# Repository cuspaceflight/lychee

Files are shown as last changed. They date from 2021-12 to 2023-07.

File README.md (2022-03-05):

# Lychee

Lychee is a HAB (high-altitude balloon) which serves two main purposes:
- An induction project for new members looking to get hands-on building and launching a HAB.
- A test bed for prototype Martlet IV electronics.

## Motivation
After many years stuck in development hell, Project Strix (Martlet IV's avionics system) was ready for
hardware prototyping and flight testing. But flight testing avionics is difficult, especially on a budget;
so we decided to return to the society's roots and bring back our dormant HAB program.

With rough designs already complete for Martlet IV's eventual launch, we decided to port the flight
computer into a less modular form factor and consolidate modules, to create an extensible dual-board
architecture that allows us to test both fundamental system hardware and prototype future modules through
an expansion slot.

## Aims
The launch aims to test several key features and subsystems of the design ahead of construction of
final Project Strix flight hardware. In summary, these are:
- understand the embedded systems prototyping and development process for the STM32 + ChibiOS/RT stack
- perform real-time altimetry through a combination of
  - 2x redudant barometers
  - 1x 6-DoF IMU
  - 1x GPS
- relay telemetry through our custom ISM-band radio system
- verify the electrical performance of our 'blackbox' flight data recorder

## Using This Repository
This repository contains the electrical and software design files for the project. PCB designs were created
in KiCad 6, and the software was written for ChibiOS/RT. To install the dependency submodules, run
`git submodule update --init` from the root directory.

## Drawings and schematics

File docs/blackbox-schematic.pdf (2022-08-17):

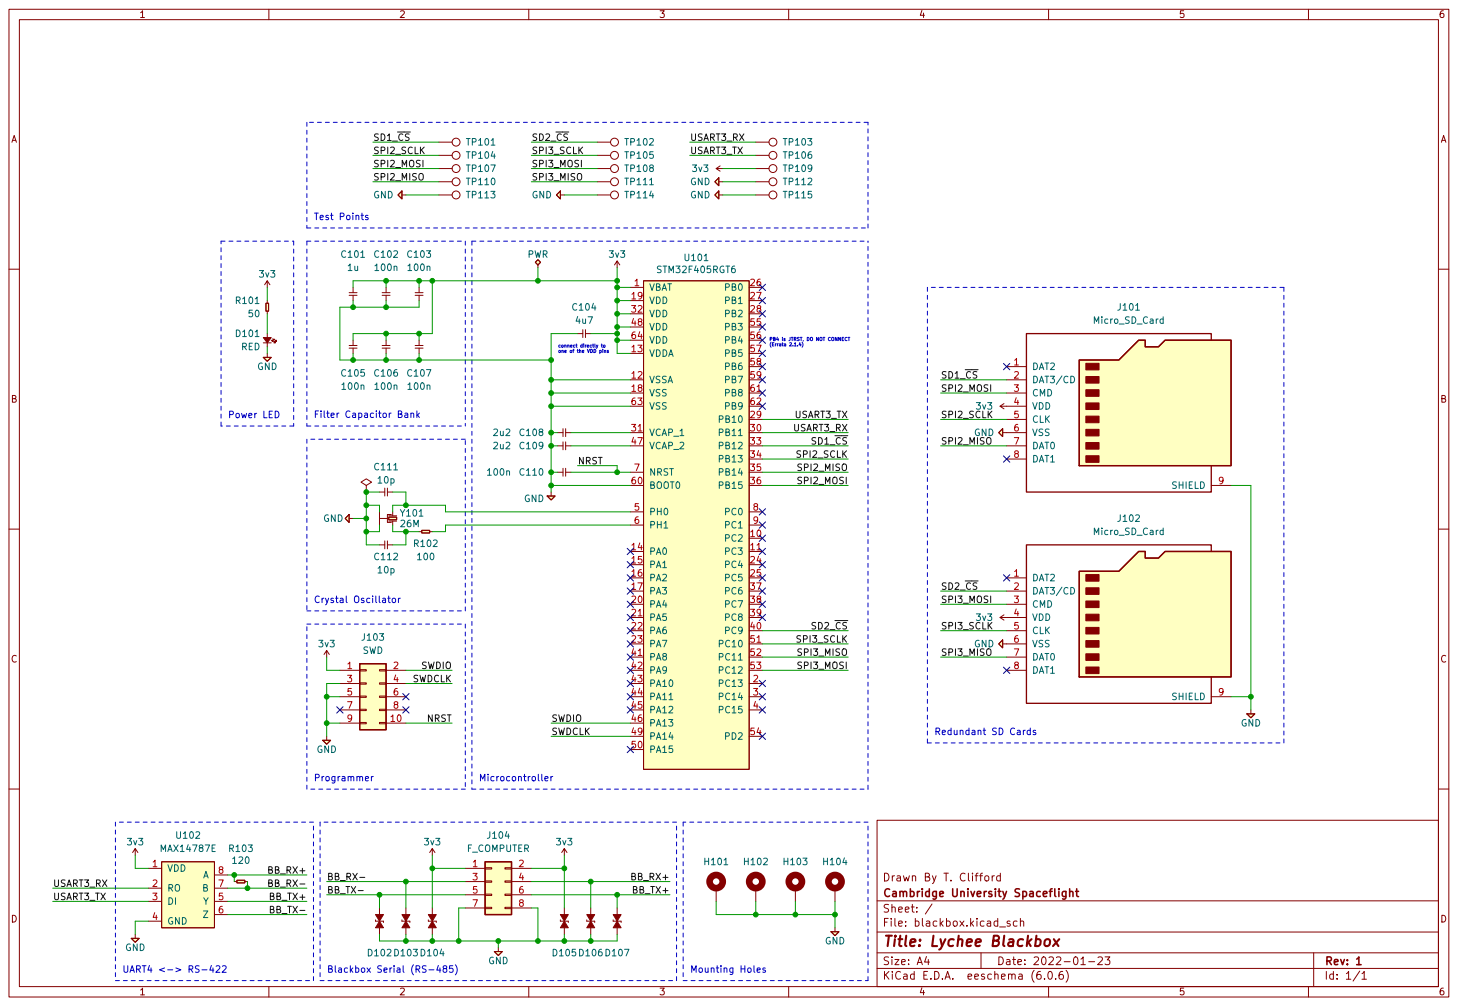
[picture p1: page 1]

PB4 is JTRST, DO NOT CONNECT

one of the VDD pins Power LED
100n GND

3 | | 4 6 8

Drawn By T. Clifford
File: blackbox.kicad_sch Sheet: / Cambridge University Spaceflight

Id: 1/1 Title: Lychee Blackbox

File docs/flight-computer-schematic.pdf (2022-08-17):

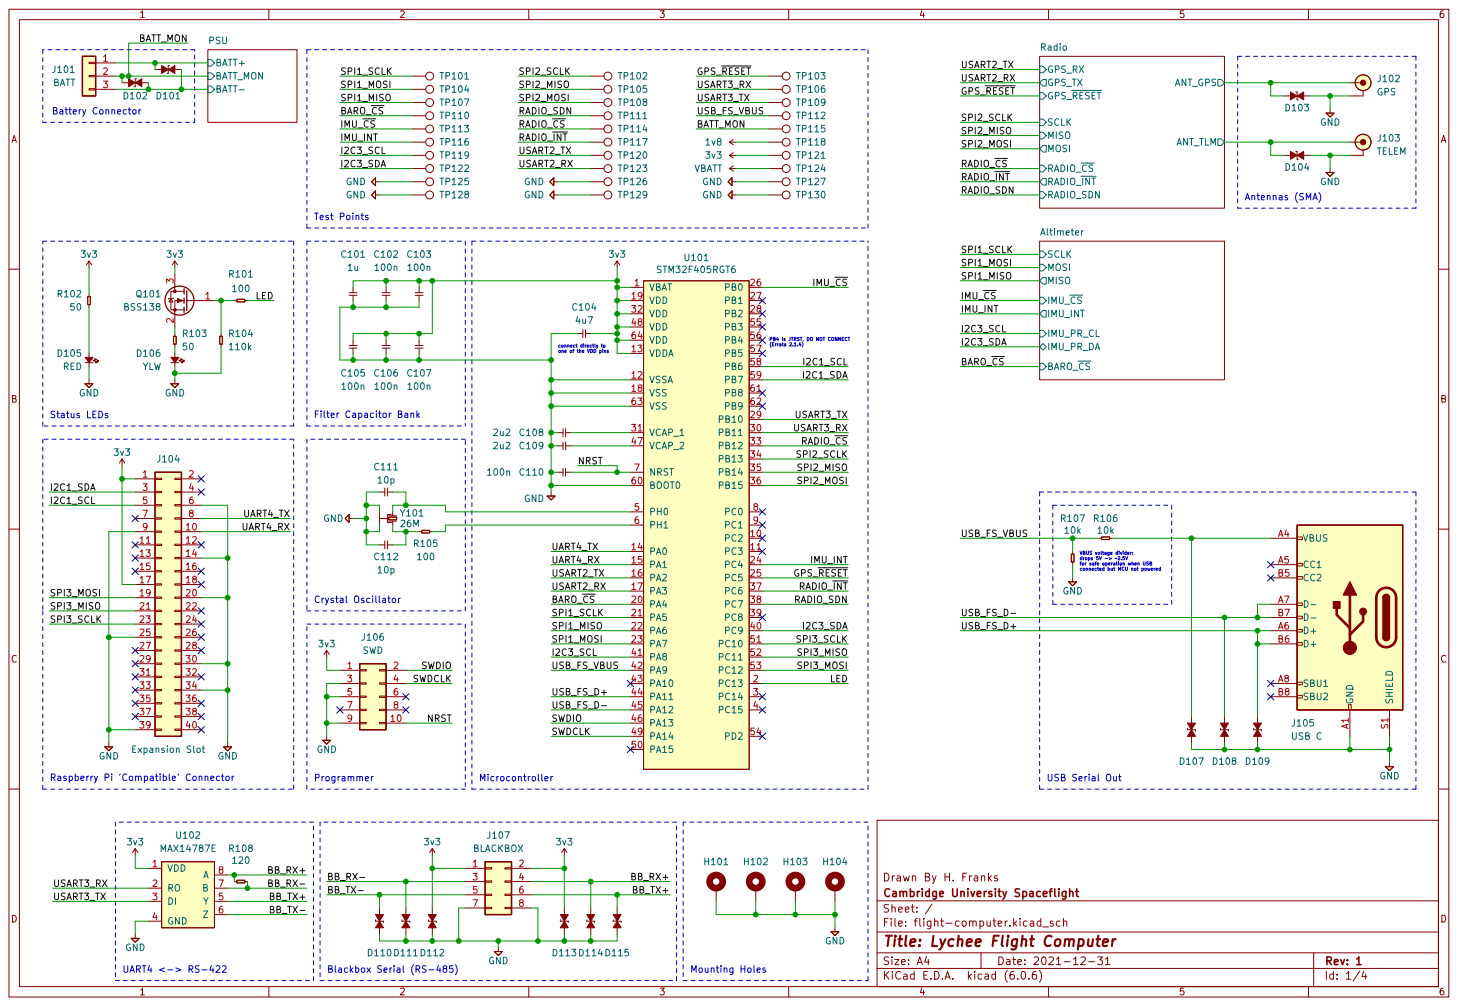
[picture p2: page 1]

SCLK MISO MOSI RADIO_~{INT} GPS_TX Radio BARO_~{CS}

RADIO_~{CS} SPI1_MOSI
Test Points Filter Capacitor Bank

(Errata 2.1.4) Raspberry Pi 'Compatible' Connector
D105 RED

PB4 is JTRST, DO NOT CONNECT

VBUS voltage divider: drops 5V -> ~2.5V

for safe operation when USB

connected but MCU not powered Crystal Oscillator

Drawn By H. Franks
File: flight-computer.kicad_sch Sheet: / Cambridge University Spaceflight

Id: 1/4 Title: Lychee Flight Computer

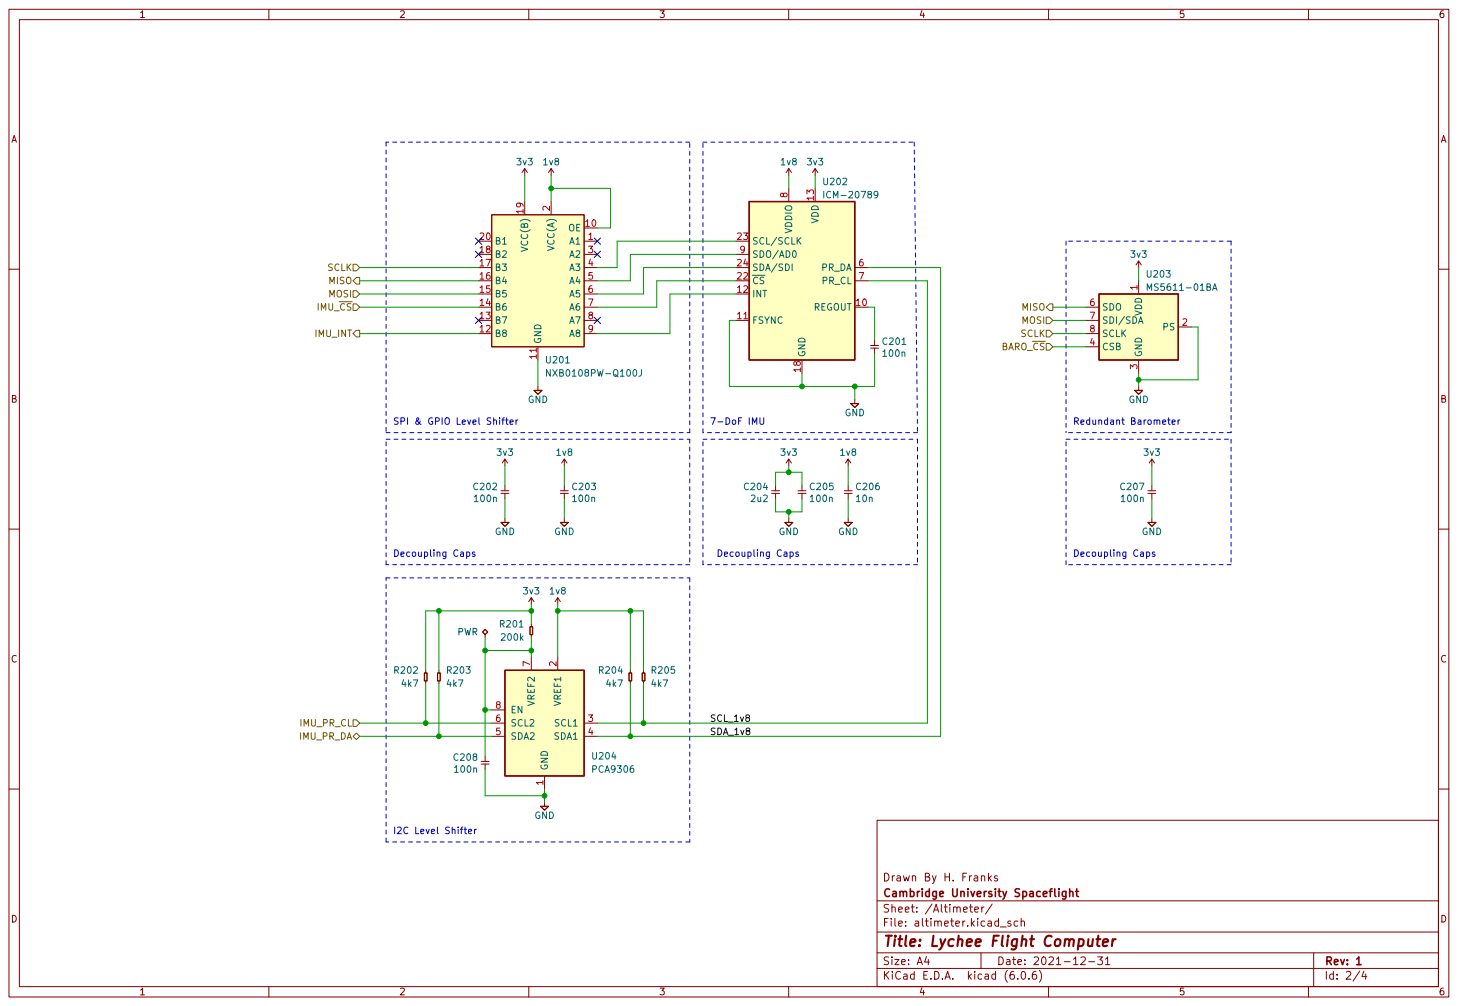
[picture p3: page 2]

3 CSB 4 SDO 6 SDI/SDA 7 SCLK 8 U203 MS5611-01BA REGOUT 10 FSYNC 11

Drawn By H. Franks
File: altimeter.kicad_sch Sheet: /Altimeter/ Cambridge University Spaceflight

Id: 2/4 Title: Lychee Flight Computer

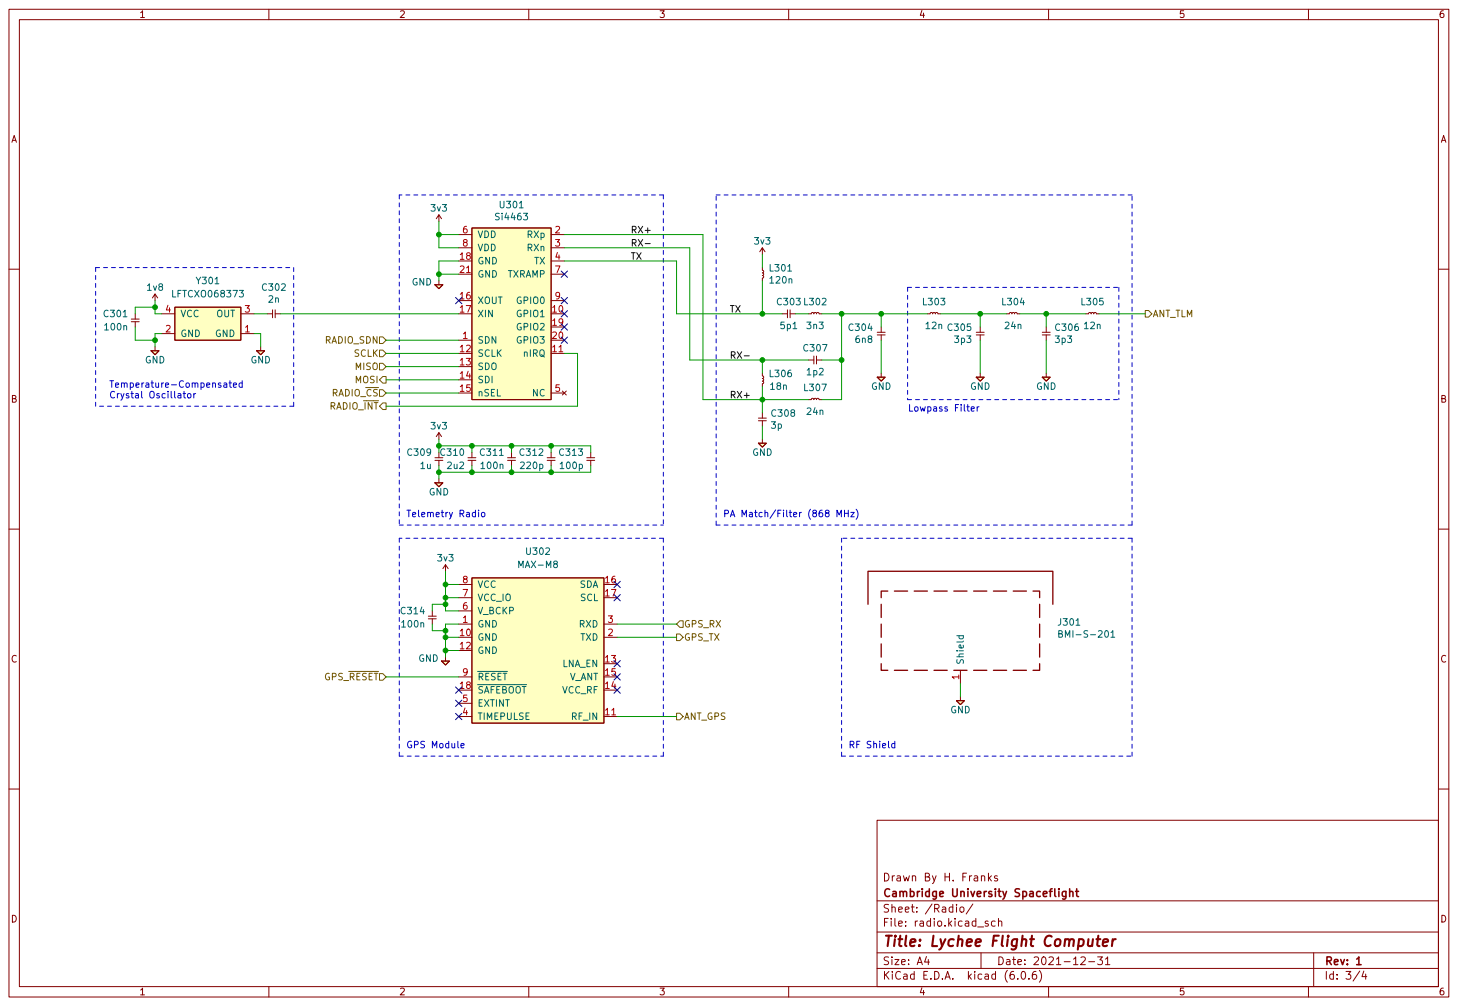
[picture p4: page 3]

TXRX- RX+ Telemetry Radio

Lowpass Filter RF Shield PA Match/Filter (868 MHz) GPS Module

Drawn By H. Franks
File: radio.kicad_sch Sheet: /Radio/ Cambridge University Spaceflight

Id: 3/4 Title: Lychee Flight Computer

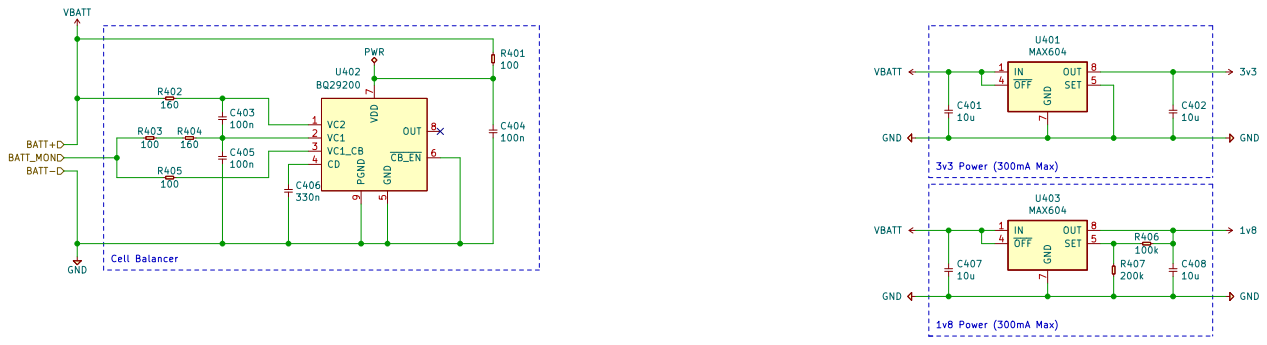
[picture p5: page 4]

File: psu.kicad_sch Sheet: /PSU/ Cambridge University Spaceflight

Id: 4/4 Title: Lychee Flight Computer

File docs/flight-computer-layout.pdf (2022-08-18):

MISO | MOSI | 0

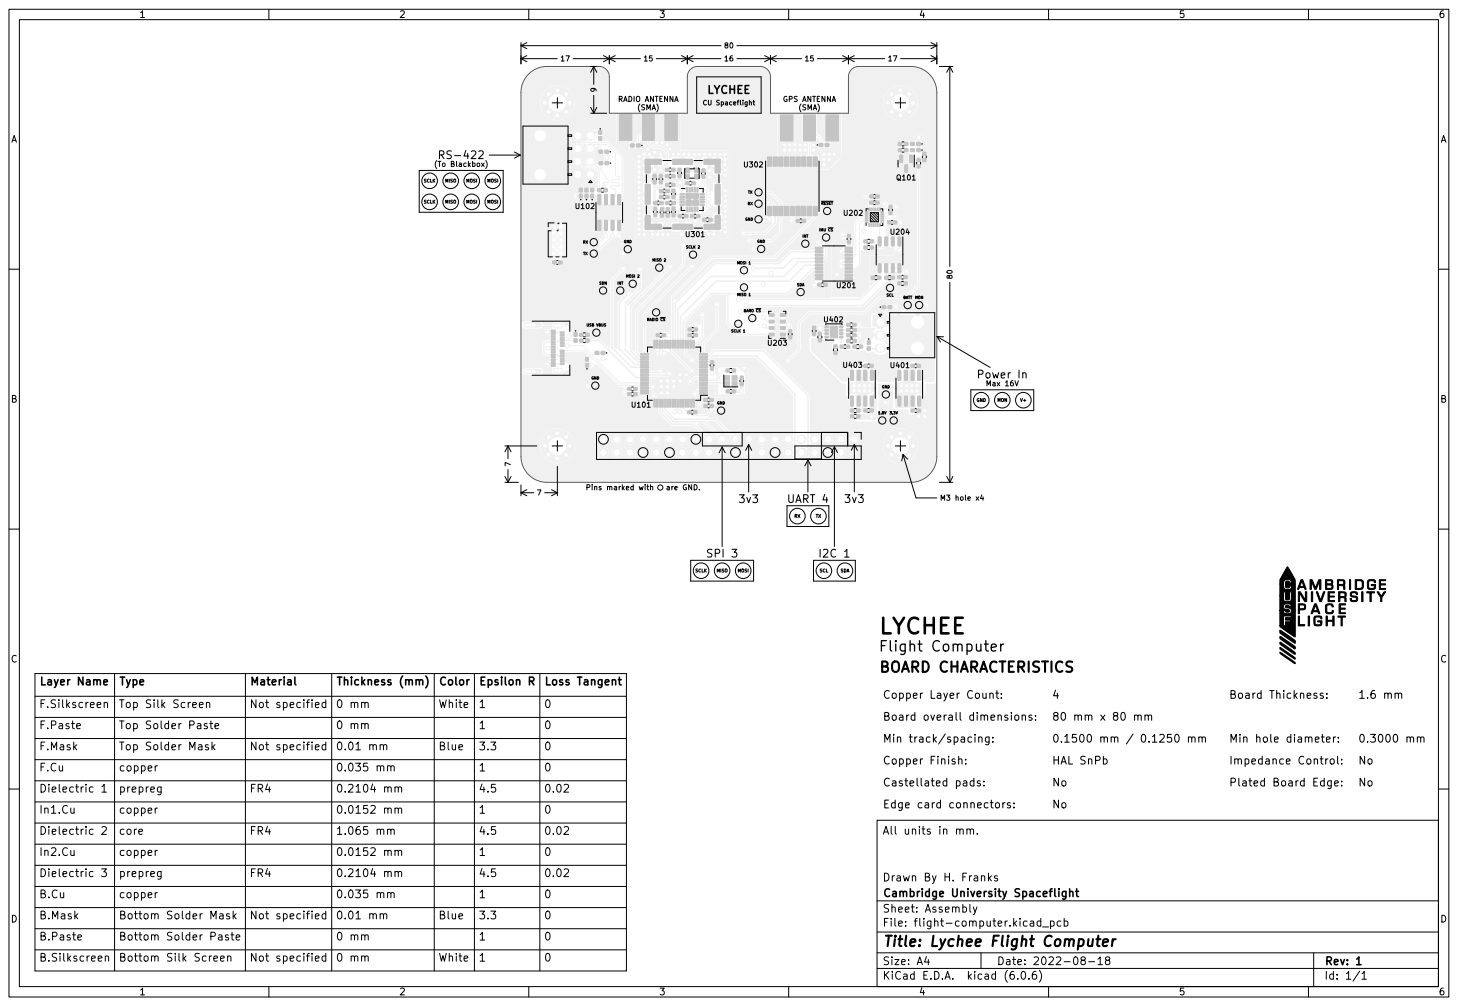
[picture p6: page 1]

CU Spaceflight
Pins marked with are GND. 1

MOSI Blue Top Solder Paste

0 Material Bottom Solder Paste
0 mm | | 1 Top Solder Mask

Thickness (mm) 0.01 mm | 1 FR4

Dielectric 1 | | 0.2104 mm | | 4.5
In1.Cu | copper | | White | | 0 | Drawn By H. Franks All units in mm. B.Paste
Dielectric 2 | | 1.065 mm | | 4.5

B.Mask | prepreg | | | 4.5 | 0.02

Cambridge University Spaceflight
Sheet: Assembly
File: flight-computer.kicad_pcb
Id: 1/1 Title: Lychee Flight Computer

0.035 mm | | | 0
0.01 mm | | 3.3 | 0

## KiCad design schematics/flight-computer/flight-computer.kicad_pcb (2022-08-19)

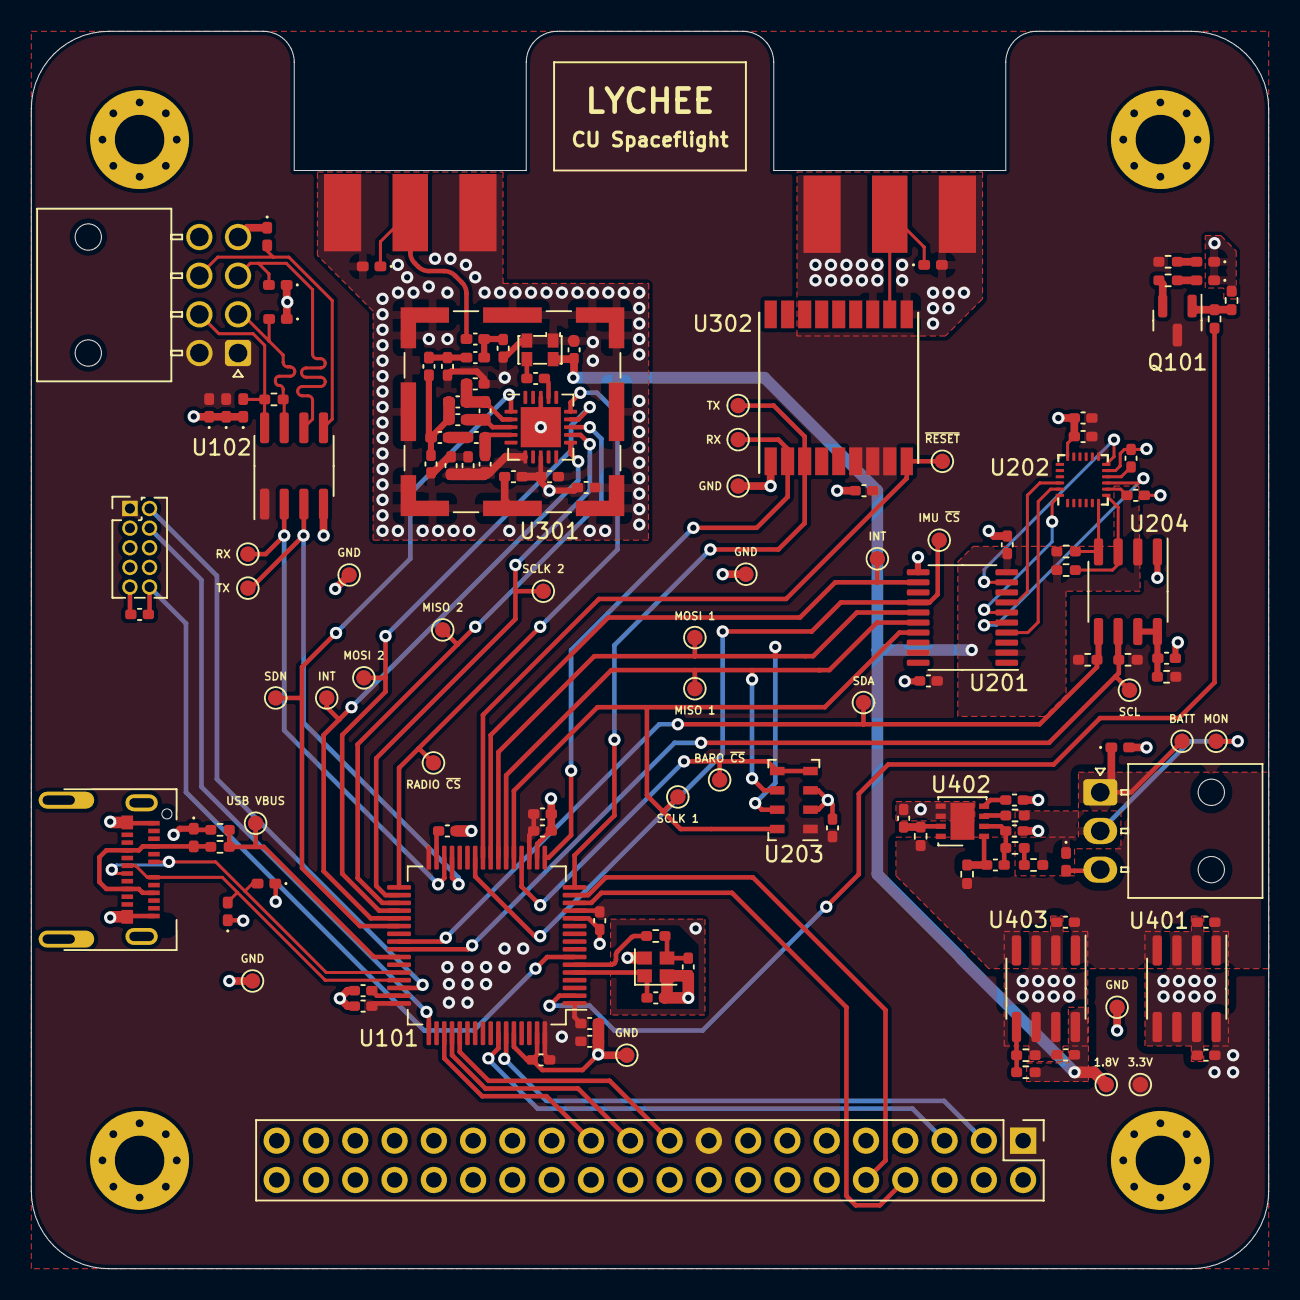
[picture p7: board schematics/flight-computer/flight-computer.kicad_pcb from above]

Board: 4 copper layers, 80.0 x 80.0 mm, 139 parts (0 on the bottom side), 79 nets.

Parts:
1.8V, 3.3V: TestPoint
BARO ~{CS}: TestPoint
BATT: TestPoint
C101: 1µ; C_0402
C102, C103, C105, C106, C107, C110, C201, C202, C203, C205, C207, C208, C301, C311, C314, C403, C404, C405: 100n; C_0402
C104: 4µ7; C_0402
C108, C109: 2µ2; C_0402
C111, C112: 10p; C_0402
C204, C310: 2u2; C_0402
C206: 10n; C_0402
C302: 2n; C_0402
C303: 5p1; C_0402
C304: 6n8; C_0402
C305, C306: 3p3; C_0402
C307: 1p2; C_0402
C308: 3p; C_0402
C309: 1u; C_0402
C312: 220p; C_0402
C313: 100p; C_0402
C401, C402, C407, C408: 10u; C_0402
C406: 330n; C_0402
D101, D102, D103, D104, D107, D108, D109, D110, D111, D112, D113, D114, D115: D_ESD; D_0402
D105: RED; LED_0402
D106: YLW; LED_0402
GND: TestPoint
GND#2, GND#3, GND#4, GND#5, GND#6: TestPoint
H101, H102, H103, H104: MountingHole_Pad
IMU ~{CS}: TestPoint
INT: TestPoint
INT#2: TestPoint
J101: BATT; Molex_Nano-Fit_105313-1103
J102: GPS; SMA-Edge
J103: TELEM; SMA-Edge
J104: Expansion Slot; Header_RaspberryPi
J105: USB C; USB_C
J106: SWD; Header_SWD
J107: BLACKBOX; Molex_Nano-Fit_105314-1108
J301: BMI-S-201
L301: 120n; L_0402
L302: 3n3; L_0402
L303, L305: 12n; L_0402
L304, L307: 24n; L_0402
L306: 18n; L_0402
MISO 1, MISO 2: TestPoint
MON: TestPoint
MOSI 1, MOSI 2: TestPoint
Q101: BSS138
R101, R105, R401, R403, R405: 100; R_0402
R102, R103: 50; R_0402
R104: 110k; R_0402
R106, R107: 10k; R_0402
R108: 120; R_0402
R201, R407: 200k; R_0402
R202, R203, R204, R205: 4k7; R_0402
R402, R404: 160; R_0402
R406: 100k; R_0402
RADIO ~{CS}: TestPoint
RX: TestPoint
RX#2: TestPoint
SCL: TestPoint
SCLK 1, SCLK 2: TestPoint
SDA: TestPoint
SDN: TestPoint
TX: TestPoint
TX#2: TestPoint
U101: STM32F405RGT6
U102: MAX14787E
U201: NXB0108PW-Q100J
U202: ICM-20789
U203: MS5611-01BA
U204: PCA9306
U301: Si4463
U302: MAX-M8
U401, U403: MAX604
U402: BQ29200
USB VBUS: TestPoint
Y101: 26M; Xtal_SMD_2016
Y301: LFTCXO068373

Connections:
1v8: 1.8V.1, C203.2, C206.2, C301.1, C408.1, R204.2, R205.2, R406.2, U201.2 (VCC(A)), U201.10 (OE), U202.8 (VDDIO), U204.2 (VREF1), U403.8 (OUT), Y301.4 (VCC)
3v3: 3.3V.1, C101.2, C102.2, C103.2, C104.2, C105.2, C106.2, C107.2, C202.2, C204.2, C205.2, C207.2, C309.1, C310.1, C311.1, C312.1, C313.1, C314.2, C402.1, D112.2, D113.2, J104.1, J104.17, J106.1, J107.1, J107.2, L301.1, Q101.3 (D), R102.2, R201.2, R202.2, R203.2, U101.1 (VBAT), U101.13 (VDDA), U101.19 (VDD), U101.32 (VDD), U101.48 (VDD), U101.64 (VDD), U102.1 (VDD), U201.19 (VCC(B)), U202.13 (VDD), U203.1 (VDD), U301.6 (VDD), U301.8 (VDD), U302.6 (V_BCKP), U302.7 (VCC_IO), U302.8 (VCC), U401.8 (OUT)
/Altimeter/SCL_1v8: R205.1, U202.7 (PR_CL), U204.3 (SCL1)
/Altimeter/SDA_1v8: R204.1, U202.6 (PR_DA), U204.4 (SDA1)
/BARO_~CS: BARO ~{CS}.1, U101.20 (PA4), U203.4 (CSB), U203.5 (CSB)
/BATT_MON: D102.1, J101.2, MON.1, R403.1, R405.1
/BB_RX+: D114.2, J107.4, R108.1, U102.8 (A)
/BB_RX-: D111.2, J107.3, R108.2, U102.7 (B)
/BB_TX+: D115.2, J107.6, U102.5 (Y)
/BB_TX-: D110.2, J107.5, U102.6 (Z)
/GPS_~RESET: U101.25 (PC5), U302.9 (~RESET)
/I2C1_SCL: J104.5, U101.58 (PB6)
/I2C1_SDA: J104.3, U101.59 (PB7)
/I2C3_SCL: R202.1, SCL.1, U101.41 (PA8), U204.6 (SCL2)
/I2C3_SDA: R203.1, SDA.1, U101.40 (PC9), U204.5 (SDA2)
/IMU_INT: INT#2.1, U101.24 (PC4), U201.12 (B8)
/IMU_~CS: IMU ~{CS}.1, U101.26 (PB0), U201.14 (B6)
/LED: R101.1, U101.2 (PC13)
/NRST: C110.2, J106.10, U101.7 (NRST)
/RADIO_SDN: SDN.1, U101.38 (PC7), U301.1 (SDN)
/RADIO_~CS: RADIO ~{CS}.1, U101.33 (PB12), U301.15 (nSEL)
/RADIO_~INT: INT.1, U101.37 (PC6), U301.11 (nIRQ)
/Radio/ANT_GPS: D103.1, J102.1 (RF), U302.11 (RF_IN)
/Radio/ANT_TLM: D104.1, J103.1 (RF), L305.2
/Radio/RX+: C308.1, L306.2, L307.1, U301.2 (RXp)
/Radio/RX-: C307.1, L306.1, U301.3 (RXn)
/Radio/TX: C303.1, L301.2, U301.4 (TX)
/SPI1_MISO: MISO 1.1, U101.22 (PA6), U201.16 (B4), U203.6 (SDO)
/SPI1_MOSI: MOSI 1.1, U101.23 (PA7), U201.15 (B5), U203.7 (SDI/SDA)
/SPI1_SCLK: SCLK 1.1, U101.21 (PA5), U201.17 (B3), U203.8 (SCLK)
/SPI2_MISO: MISO 2.1, U101.35 (PB14), U301.13 (SDO)
/SPI2_MOSI: MOSI 2.1, U101.36 (PB15), U301.14 (SDI)
/SPI2_SCLK: SCLK 2.1, U101.34 (PB13), U301.12 (SCLK)
/SPI3_MISO: J104.21, U101.52 (PC11)
/SPI3_MOSI: J104.19, U101.53 (PC12)
/SPI3_SCLK: J104.23, U101.51 (PC10)
/SWDCLK: J106.4, U101.49 (PA14)
/SWDIO: J106.2, U101.46 (PA13)
/UART4_RX: J104.10, U101.15 (PA1)
/UART4_TX: J104.8, U101.14 (PA0)
/USART2_RX: RX#2.1, U101.17 (PA3), U302.2 (TXD)
/USART2_TX: TX.1, U101.16 (PA2), U302.3 (RXD)
/USART3_RX: RX.1, U101.30 (PB11), U102.2 (RO)
/USART3_TX: TX#2.1, U101.29 (PB10), U102.3 (DI)
/USB_FS_D+: D109.2, J105.A6 (D+), J105.B6 (D+), U101.44 (PA11)
/USB_FS_D-: D108.2, J105.A7 (D-), J105.B7 (D-), U101.45 (PA12)
/USB_FS_VBUS: R106.1, R107.2, U101.42 (PA9), USB VBUS.1
GND: C101.1, C102.1, C103.1, C104.1, C105.1, C106.1, C107.1, C108.1, C109.1, C110.1, C111.1, C112.1, C201.1, C202.1, C203.1, C204.1, C205.1, C206.1, C207.1, C208.1, C301.2, C304.2, C305.2, C306.2, C308.2, C309.2, C310.2, C311.2, C312.2, C313.2, C314.1, C401.2, C402.2, C404.2, C405.2, C406.2, C407.2, C408.2, D101.2, D102.2, D103.2, D104.2, D105.1, D106.1, D107.1, D108.1, D109.1, D110.1, D111.1, D112.1, D113.1, D114.1, D115.1, GND.1, GND#2.1, GND#3.1, GND#4.1, GND#5.1, GND#6.1, H101.1, H102.1, H103.1, H104.1, J101.3, J102.2 (GND), J103.2 (GND), J104.6, J104.9, J104.14, J104.20, J104.25, J104.30, J104.34, J104.39, J105.A1 (GND), J105.A12 (GND), J105.B1 (GND), J105.B12 (GND), J105.S1 (SHIELD), J106.3, J106.5, J106.9, J107.7, J107.8, J301.1 (Shield), R104.1, R107.1, R407.2, U101.12 (VSSA), U101.18 (VSS), U101.60 (BOOT0), U101.63 (VSS), U102.4 (GND), U201.11 (GND), U202.11 (FSYNC), U202.18 (GND), U203.2 (PS), U203.3 (GND), U204.1 (GND), U301.18 (GND), U301.21 (GND), U302.1 (GND), U302.10 (GND), U302.12 (GND), U401.2 (GND), U401.3 (GND), U401.5 (SET), U401.6 (GND), U401.7 (GND), U402.5 (GND), U402.6 (~CB_EN), U402.9 (PGND), U403.2 (GND), U403.3 (GND), U403.6 (GND), U403.7 (GND), Y101.2, Y101.4, Y301.1 (GND), Y301.2 (GND)
unnamed: C108.2, U101.31 (VCAP_1)
unnamed: C109.2, U101.47 (VCAP_2)
unnamed: C111.2, U101.5 (PH0), Y101.1
unnamed: C112.2, R105.1, Y101.3
unnamed: C201.2, U202.10 (REGOUT)
unnamed: C208.2, R201.1, U204.7 (VREF2), U204.8 (EN)
unnamed: C302.1, Y301.3 (OUT)
unnamed: C302.2, U301.17 (XIN)
unnamed: C303.2, L302.1
unnamed: C304.1, C307.2, L302.2, L303.1, L307.2
unnamed: C305.1, L303.2, L304.1
unnamed: C306.1, L304.2, L305.1
unnamed: C403.1, R402.2, U402.1 (VC2)
unnamed: C403.2, C405.1, R404.2, U402.2 (VC1)
unnamed: C404.1, R401.2, U402.7 (VDD)
unnamed: C406.1, U402.4 (CD)
unnamed: D105.2, R102.1
unnamed: D106.2, R103.1
unnamed: D107.2, J105.A4 (VBUS), J105.A9 (VBUS), J105.B4 (VBUS), J105.B9 (VBUS), R106.2
unnamed: Q101.1 (G), R101.2, R104.2
unnamed: Q101.2 (S), R103.2
unnamed: R105.2, U101.6 (PH1)
unnamed: R403.2, R404.1
unnamed: R405.2, U402.3 (VC1_CB)
unnamed: R406.1, R407.1, U403.5 (SET)
unnamed: U201.4 (A3), U202.23 (SCL/SCLK)
unnamed: U201.5 (A4), U202.9 (SDO/AD0)
unnamed: U201.6 (A5), U202.24 (SDA/SDI)
unnamed: U201.7 (A6), U202.22 (~CS)
unnamed: U201.9 (A8), U202.12 (INT)
VBATT: BATT.1, C401.1, C407.1, D101.1, J101.1, R401.1, R402.1, U401.1 (IN), U401.4 (~OFF), U403.1 (IN), U403.4 (~OFF)

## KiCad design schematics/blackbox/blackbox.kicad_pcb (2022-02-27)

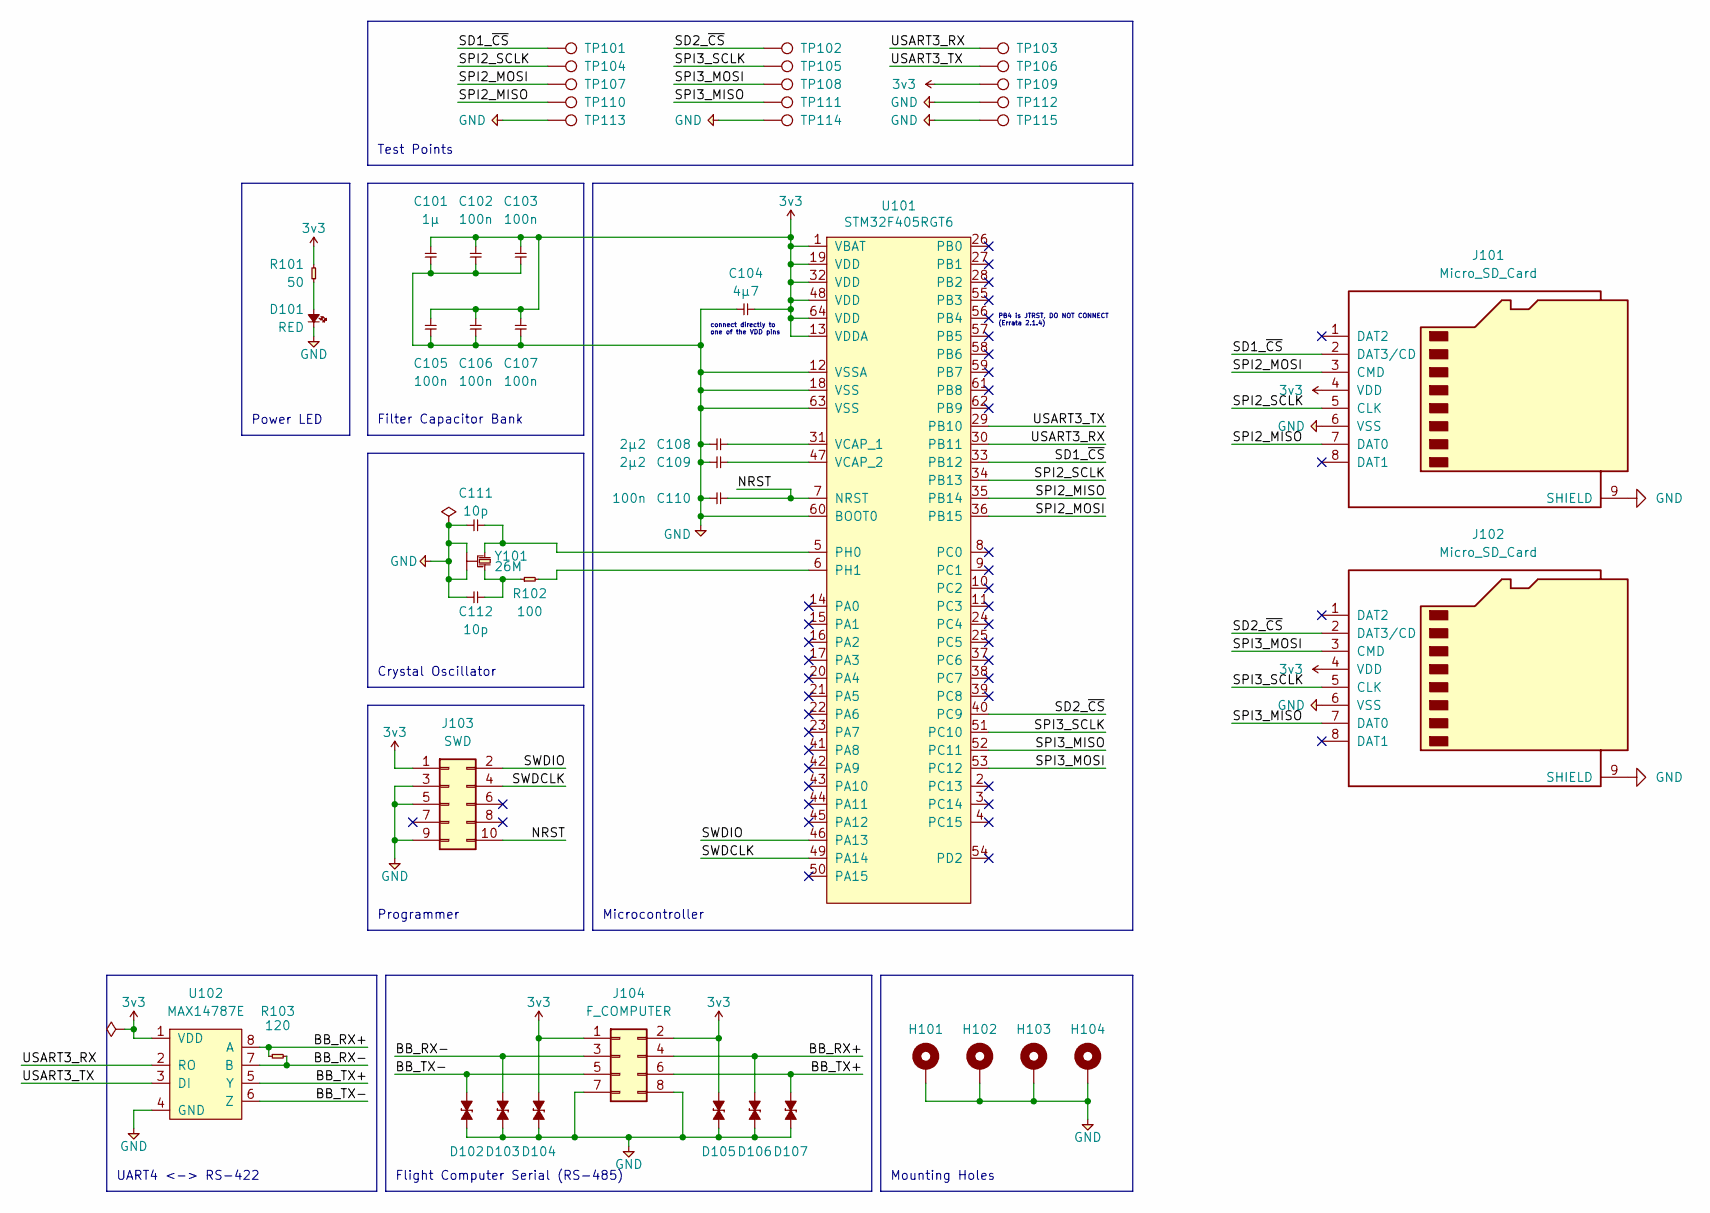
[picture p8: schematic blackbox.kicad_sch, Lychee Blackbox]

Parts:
C101: 1µ; C_0402; Farnell 1759436
C102, C103, C105, C106, C107, C110: 100n; C_0402; Farnell 2496771
C104: 4µ7; C_0402; Farnell 2211173
C108, C109: 2µ2; C_0402; Farnell 2362088
C111, C112: 10p; C_0402; Farnell 2494183
D101: RED; LED_0402; Farnell 3796306
D102, D103, D104, D105, D106, D107: D_ESD; D_0402; Farnell 2368169
H101, H102, H103, H104: MountingHole_Pad
J101, J102: Micro_SD_Card; microSD_HC_Wuerth_693072010801; Farnell 1344008
J103: SWD; Header_SWD; Farnell 2856426
J104: F_COMPUTER; Molex_Nano-Fit_105314-1108
R101: 50; R_0402; Farnell 3544456
R102: 100; R_0402; Farnell 2447095
R103: 120; R_0402; Farnell 2447103
TP101, TP102, TP103, TP104, TP105, TP106, TP107, TP108, TP109, TP110, TP111, TP112, TP113, TP114, TP115: TestPoint
U101: STM32F405RGT6; Farnell 2064363
U102: MAX14787E; Farnell 2528531
Y101: 26M; Xtal_SMD_2016; Farnell 2506952

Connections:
3v3: C101.2, C102.2, C103.2, C104.2, C105.2, C106.2, C107.2, D104.2, D105.2, J101.4 (VDD), J102.4 (VDD), J103.1, J104.1, J104.2, R101.2, TP109.1, U101.1 (VBAT), U101.13 (VDDA), U101.19 (VDD), U101.32 (VDD), U101.48 (VDD), U101.64 (VDD), U102.1 (VDD)
/BB_RX+: D106.2, J104.4, R103.1, U102.8 (A)
/BB_RX-: D103.2, J104.3, R103.2, U102.7 (B)
/BB_TX+: D107.2, J104.6, U102.5 (Y)
/BB_TX-: D102.2, J104.5, U102.6 (Z)
/NRST: C110.2, J103.10, U101.7 (NRST)
/SD1_~CS: J101.2 (DAT3/CD), TP101.1, U101.33 (PB12)
/SD2_~CS: J102.2 (DAT3/CD), TP102.1, U101.40 (PC9)
/SPI2_MISO: J101.7 (DAT0), TP110.1, U101.35 (PB14)
/SPI2_MOSI: J101.3 (CMD), TP107.1, U101.36 (PB15)
/SPI2_SCLK: J101.5 (CLK), TP104.1, U101.34 (PB13)
/SPI3_MISO: J102.7 (DAT0), TP111.1, U101.52 (PC11)
/SPI3_MOSI: J102.3 (CMD), TP108.1, U101.53 (PC12)
/SPI3_SCLK: J102.5 (CLK), TP105.1, U101.51 (PC10)
/SWDCLK: J103.4, U101.49 (PA14)
/SWDIO: J103.2, U101.46 (PA13)
/USART3_RX: TP103.1, U101.30 (PB11), U102.2 (RO)
/USART3_TX: TP106.1, U101.29 (PB10), U102.3 (DI)
GND: C101.1, C102.1, C103.1, C104.1, C105.1, C106.1, C107.1, C108.1, C109.1, C110.1, C111.1, C112.1, D101.1, D102.1, D103.1, D104.1, D105.1, D106.1, D107.1, H101.1, H102.1, H103.1, H104.1, J101.6 (VSS), J101.9 (SHIELD), J102.6 (VSS), J102.9 (SHIELD), J103.3, J103.5, J103.9, J104.7, J104.8, TP112.1, TP113.1, TP114.1, TP115.1, U101.12 (VSSA), U101.18 (VSS), U101.60 (BOOT0), U101.63 (VSS), U102.4 (GND), Y101.2, Y101.4
unnamed: C108.2, U101.31 (VCAP_1)
unnamed: C109.2, U101.47 (VCAP_2)
unnamed: C111.2, U101.5 (PH0), Y101.1
unnamed: C112.2, R102.1, Y101.3
unnamed: D101.2, R101.1
unnamed: R102.2, U101.6 (PH1)

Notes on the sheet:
Flight Computer Serial (RS-485)
Power LED
Filter Capacitor Bank
PB4 is JTRST, DO NOT CONNECT (Errata 2.1.4)
Mounting Holes
Test Points
Crystal Oscillator
UART4 <-> RS-422
Programmer
connect directly to one of the VDD pins
Microcontroller

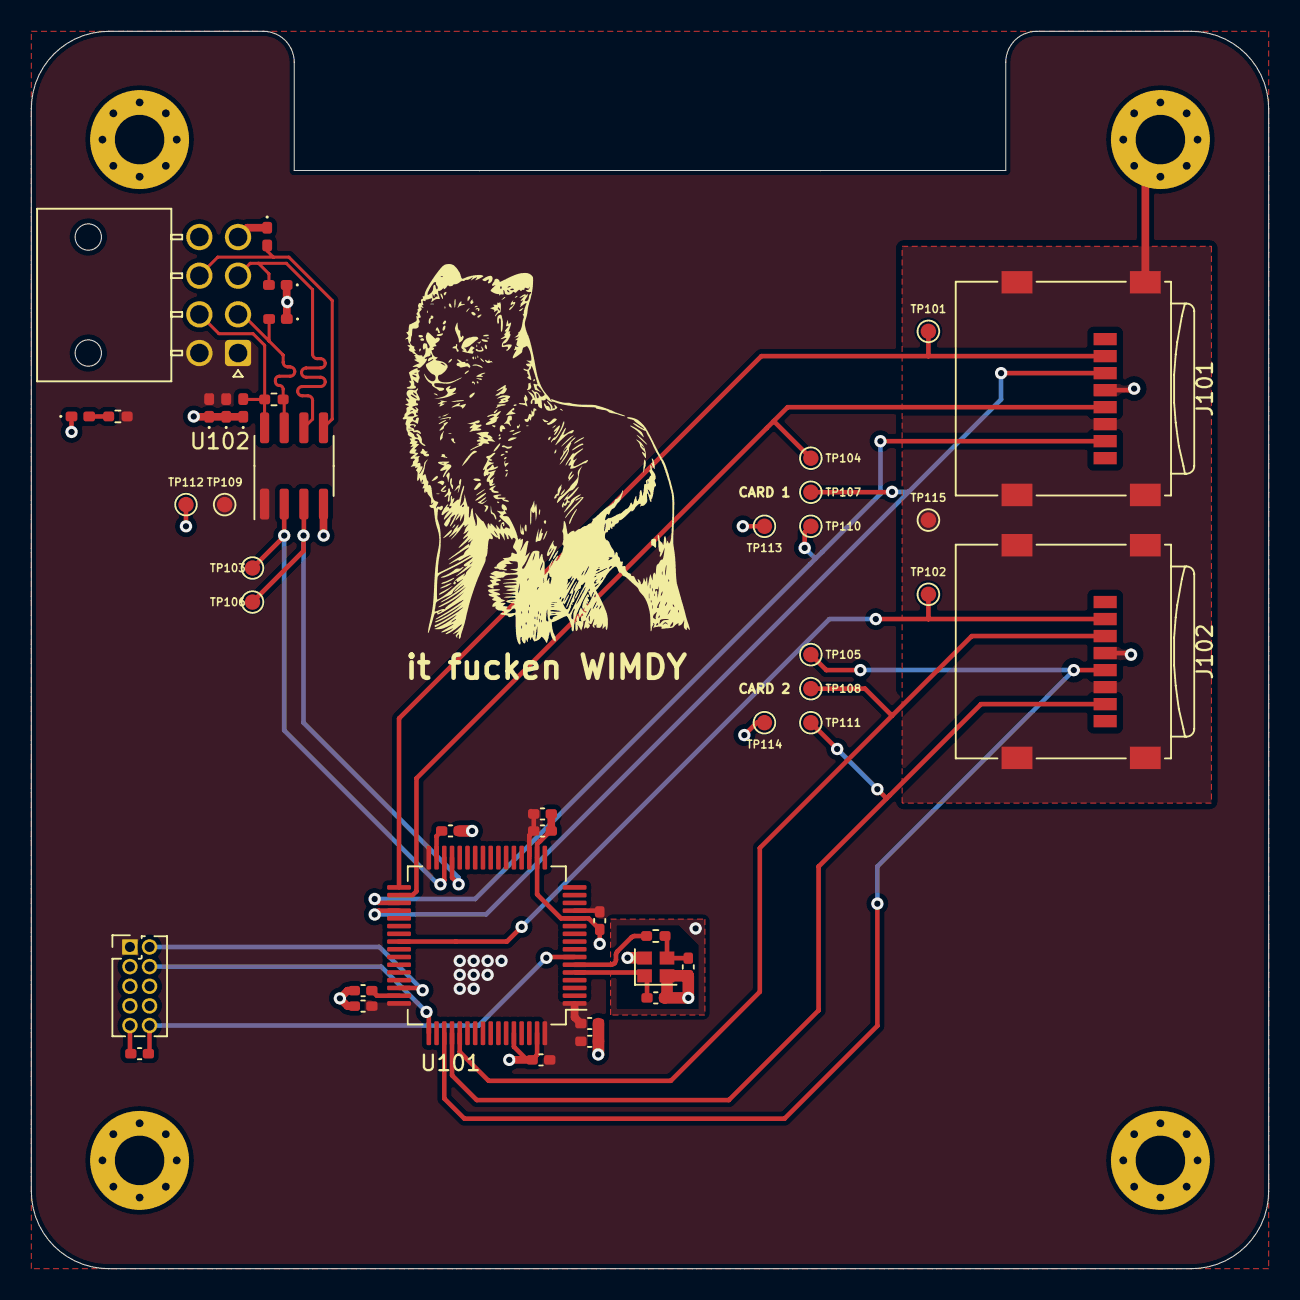
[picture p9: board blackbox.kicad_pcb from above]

Board: 4 copper layers, 80.0 x 80.0 mm, 48 parts (0 on the bottom side), 25 nets.

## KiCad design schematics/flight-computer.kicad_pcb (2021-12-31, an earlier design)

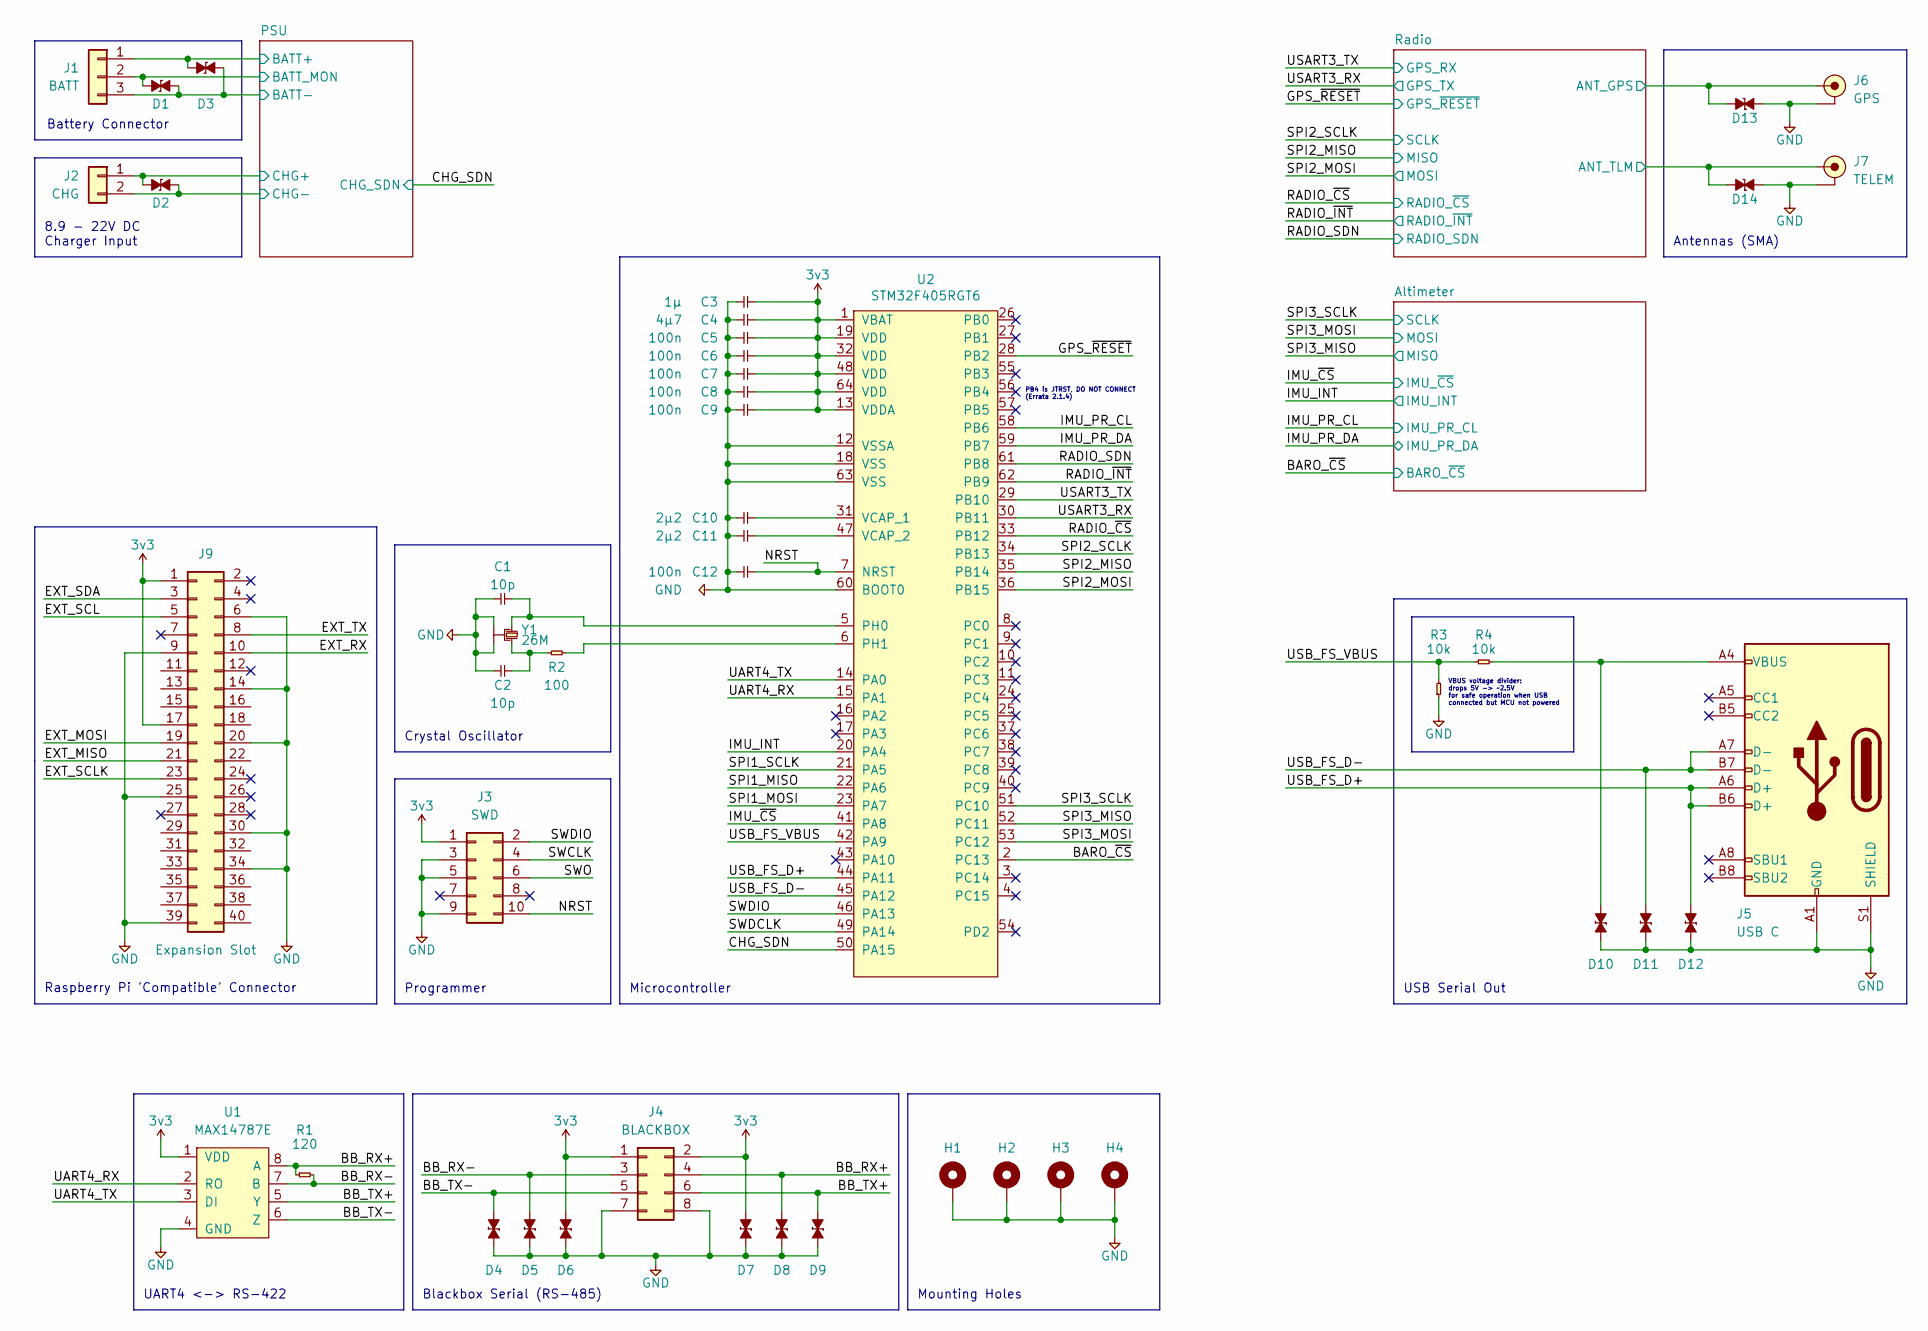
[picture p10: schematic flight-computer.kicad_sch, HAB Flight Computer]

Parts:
C1, C2: 10p; C_0402
C3: 1µ; C_0402; Farnell 2496814
C4: 4µ7; C_0402; Farnell 2426952
C5, C6, C7, C8, C9, C12: 100n; C_0402; Farnell 2496771
C10, C11: 2µ2; C_0402; Farnell 2362088
D1, D2, D3, D4, D5, D6, D7, D8, D9, D10, D11, D12, D13, D14: D_ESD; D_0402; Farnell 2368169
H1, H2, H3, H4: MountingHole_Pad
J1: BATT; Molex_Nano-Fit_105313-1103; Farnell 2820685
J2: CHG; Molex_Nano-Fit_105313-1102
J3: SWD; Header_SWD
J4: BLACKBOX; Molex_Nano-Fit_105314-1108
J5: USB C; USB_C; Farnell 2990003
J6: GPS; SMA-Edge; Farnell 1608592
J7: TELEM; SMA-Edge; Farnell 1608592
J9: Expansion Slot; Header_RaspberryPi
R1: 120; R_0402
R2: 100; R_0402
R3, R4: 10k; R_0402
U1: MAX14787E; Farnell 2528531
U2: STM32F405RGT6; Farnell 2064363
Y1: 26M; Xtal-20x16; Farnell 2506952

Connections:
3v3: C3.2, C4.2, C5.2, C6.2, C7.2, C8.2, C9.2, D6.2, D7.2, J3.1, J4.1, J4.2, J9.1, J9.17, U1.1 (VDD), U2.1 (VBAT), U2.13 (VDDA), U2.19 (VDD), U2.32 (VDD), U2.48 (VDD), U2.64 (VDD); also elsewhere on the board
/BARO_~CS: U2.2 (PC13); also elsewhere on the board
/BB_RX+: D8.2, J4.4, R1.1, U1.8 (A)
/BB_RX-: D5.2, J4.3, R1.2, U1.7 (B)
/BB_TX+: D9.2, J4.6, U1.5 (Y)
/BB_TX-: D4.2, J4.5, U1.6 (Z)
/CHG_SDN: U2.50 (PA15); also elsewhere on the board
/EXT_MISO: J9.21
/EXT_MOSI: J9.19
/EXT_RX: J9.10
/EXT_SCL: J9.5
/EXT_SCLK: J9.23
/EXT_SDA: J9.3
/EXT_TX: J9.8
/GPS_~RESET: U2.28 (PB2); also elsewhere on the board
/IMU_INT: U2.20 (PA4); also elsewhere on the board
/IMU_PR_CL: U2.58 (PB6); also elsewhere on the board
/IMU_PR_DA: U2.59 (PB7); also elsewhere on the board
/IMU_~CS: U2.41 (PA8); also elsewhere on the board
/NRST: C12.2, J3.10, U2.7 (NRST)
/PSU/BATT_MON: D1.1, J1.2; also elsewhere on the board
/PSU/CHG+: D2.1, J2.1; also elsewhere on the board
/RADIO_SDN: U2.61 (PB8); also elsewhere on the board
/RADIO_~CS: U2.33 (PB12); also elsewhere on the board
/RADIO_~INT: U2.62 (PB9); also elsewhere on the board
/Radio/ANT_GPS: D13.1, J6.1 (RF); also elsewhere on the board
/Radio/ANT_TLM: D14.1, J7.1 (RF); also elsewhere on the board
/SPI1_MISO: U2.22 (PA6)
/SPI1_MOSI: U2.23 (PA7)
/SPI1_SCLK: U2.21 (PA5)
/SPI2_MISO: U2.35 (PB14); also elsewhere on the board
/SPI2_MOSI: U2.36 (PB15); also elsewhere on the board
/SPI2_SCLK: U2.34 (PB13); also elsewhere on the board
/SPI3_MISO: U2.52 (PC11); also elsewhere on the board
/SPI3_MOSI: U2.53 (PC12); also elsewhere on the board
/SPI3_SCLK: U2.51 (PC10); also elsewhere on the board
/SWCLK: J3.4
/SWDCLK: U2.49 (PA14)
/SWDIO: J3.2, U2.46 (PA13)
/SWO: J3.6
/UART4_RX: U1.2 (RO), U2.15 (PA1)
/UART4_TX: U1.3 (DI), U2.14 (PA0)
/USART3_RX: U2.30 (PB11); also elsewhere on the board
/USART3_TX: U2.29 (PB10); also elsewhere on the board
/USB_FS_D+: D12.2, J5.A6 (D+), J5.B6 (D+), U2.44 (PA11)
/USB_FS_D-: D11.2, J5.A7 (D-), J5.B7 (D-), U2.45 (PA12)
/USB_FS_VBUS: R3.2, R4.1, U2.42 (PA9)
GND: C1.1, C2.1, C3.1, C4.1, C5.1, C6.1, C7.1, C8.1, C9.1, C10.1, C11.1, C12.1, D1.2, D2.2, D3.2, D4.1, D5.1, D6.1, D7.1, D8.1, D9.1, D10.1, D11.1, D12.1, D13.2, D14.2, H1.1, H2.1, H3.1, H4.1, J1.3, J2.2, J3.3, J3.5, J3.9, J4.7, J4.8, J5.A1 (GND), J5.A12 (GND), J5.B1 (GND), J5.B12 (GND), J5.S1 (SHIELD), J6.2 (GND), J7.2 (GND), J9.6, J9.9, J9.14, J9.20, J9.25, J9.30, J9.34, J9.39, R3.1, U1.4 (GND), U2.12 (VSSA), U2.18 (VSS), U2.60 (BOOT0), U2.63 (VSS), Y1.2, Y1.4; also elsewhere on the board
unnamed: C1.2, U2.5 (PH0), Y1.1
unnamed: C2.2, R2.1, Y1.3
unnamed: C10.2, U2.31 (VCAP_1)
unnamed: C11.2, U2.47 (VCAP_2)
unnamed: D10.2, J5.A4 (VBUS), J5.A9 (VBUS), J5.B4 (VBUS), J5.B9 (VBUS), R4.2
unnamed: R2.2, U2.6 (PH1)
VBATT: D3.1, J1.1; also elsewhere on the board

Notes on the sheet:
Blackbox Serial (RS-485)
USB Serial Out
PB4 is JTRST, DO NOT CONNECT (Errata 2.1.4)
Battery Connector
Mounting Holes
Crystal Oscillator
UART4 <-> RS-422
Programmer
VBUS voltage divider: drops 5V -> ~2.5V for safe operation when USB connected but MCU not powered
Microcontroller
Raspberry Pi 'Compatible' Connector
8.9 - 22V DC Charger Input
Antennas (SMA)

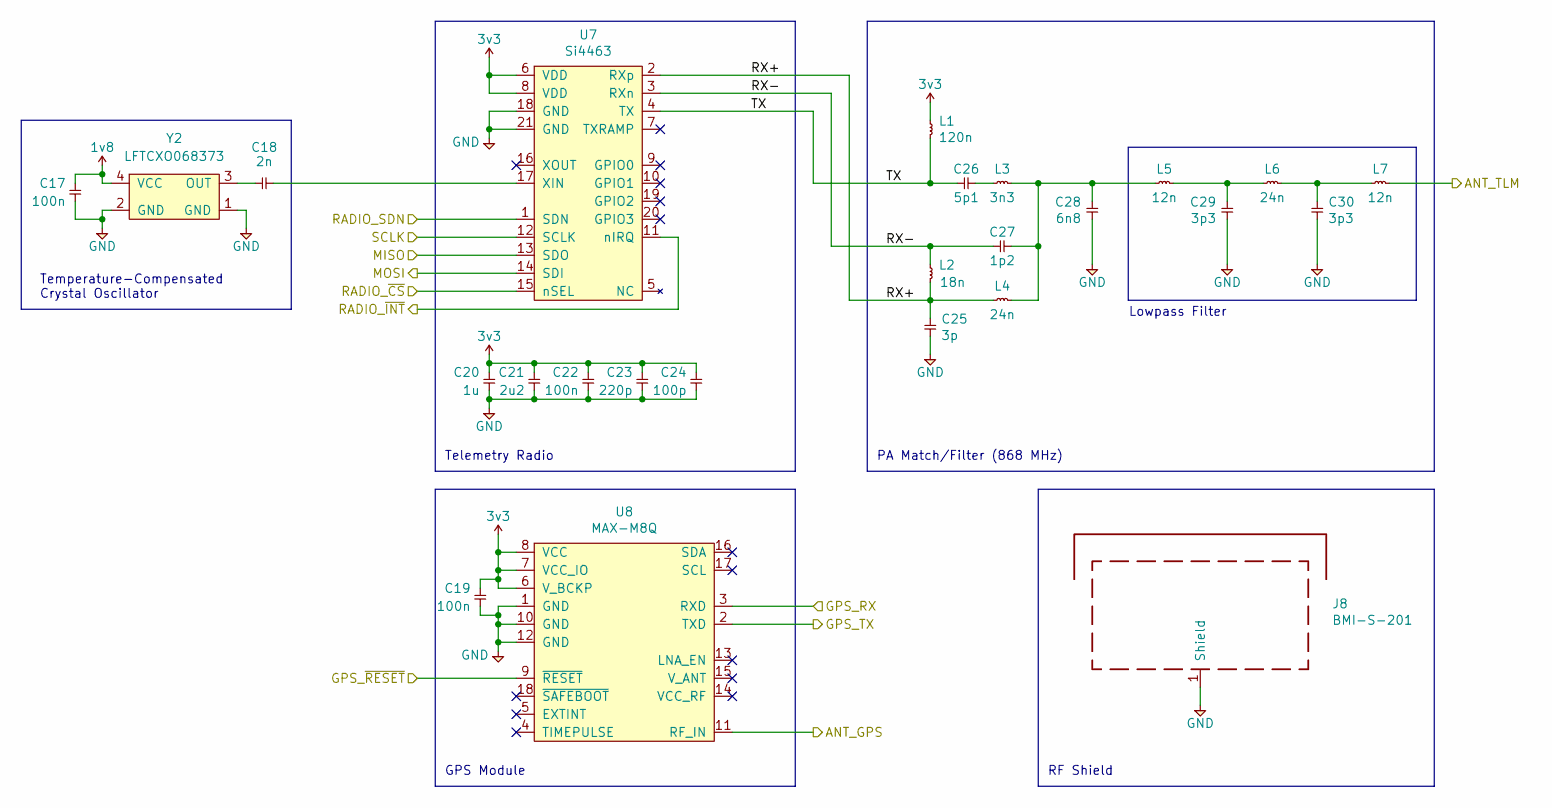
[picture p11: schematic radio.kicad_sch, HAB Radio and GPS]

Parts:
C17, C19, C22: 100n; C_0402
C18: 2n; C_0402
C20: 1u; C_0402
C21: 2u2; C_0402
C23: 220p; C_0402
C24: 100p; C_0402
C25: 3p; C_0402
C26: 5p1; C_0402
C27: 1p2; C_0402
C28: 6n8; C_0402
C29, C30: 3p3; C_0402
J8: BMI-S-201
L1: 120n; L_0402
L2: 18n; L_0402
L3: 3n3; L_0402
L4, L6: 24n; L_0402
L5, L7: 12n; L_0402
U7: Si4463; Farnell 2462637
U8: MAX-M8Q
Y2: LFTCXO068373; Farnell 2627327

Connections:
1v8: C17.1, Y2.4 (VCC); also elsewhere on the board
3v3: C19.2, C20.1, C21.1, C22.1, C23.1, C24.1, L1.1, U7.6 (VDD), U7.8 (VDD), U8.6 (V_BCKP), U8.7 (VCC_IO), U8.8 (VCC); also elsewhere on the board
/GPS_~RESET: U8.9 (~RESET); also elsewhere on the board
/RADIO_SDN: U7.1 (SDN); also elsewhere on the board
/RADIO_~CS: U7.15 (nSEL); also elsewhere on the board
/RADIO_~INT: U7.11 (nIRQ); also elsewhere on the board
/Radio/ANT_GPS: U8.11 (RF_IN); also elsewhere on the board
/Radio/ANT_TLM: L7.2; also elsewhere on the board
/Radio/RX+: C25.1, L2.2, L4.1, U7.2 (RXp)
/Radio/RX-: C27.1, L2.1, U7.3 (RXn)
/Radio/TX: C26.1, L1.2, U7.4 (TX)
/SPI2_MISO: U7.13 (SDO); also elsewhere on the board
/SPI2_MOSI: U7.14 (SDI); also elsewhere on the board
/SPI2_SCLK: U7.12 (SCLK); also elsewhere on the board
/USART3_RX: U8.2 (TXD); also elsewhere on the board
/USART3_TX: U8.3 (RXD); also elsewhere on the board
GND: C17.2, C19.1, C20.2, C21.2, C22.2, C23.2, C24.2, C25.2, C28.2, C29.2, C30.2, J8.1 (Shield), U7.18 (GND), U7.21 (GND), U8.1 (GND), U8.10 (GND), U8.12 (GND), Y2.1 (GND), Y2.2 (GND); also elsewhere on the board
unnamed: C18.1, Y2.3 (OUT)
unnamed: C18.2, U7.17 (XIN)
unnamed: C26.2, L3.1
unnamed: C27.2, C28.1, L3.2, L4.2, L5.1
unnamed: C29.1, L5.2, L6.1
unnamed: C30.1, L6.2, L7.1

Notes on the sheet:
PA Match/Filter (868 MHz)
Lowpass Filter
GPS Module
Telemetry Radio
Temperature-Compensated Crystal Oscillator
RF Shield

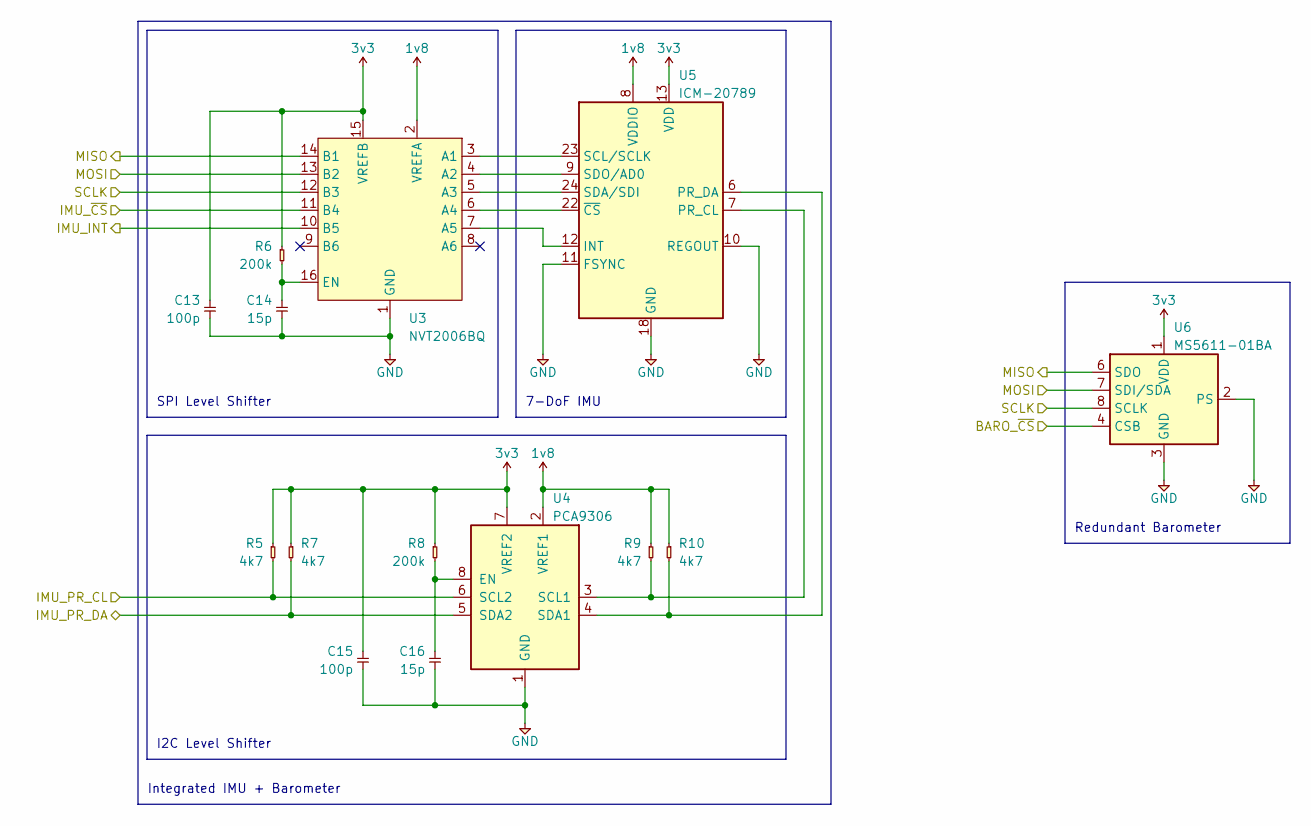
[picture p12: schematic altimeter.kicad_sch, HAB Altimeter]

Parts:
C13, C15: 100p; C_0402
C14, C16: 15p; C_0402
R5, R7, R9, R10: 4k7; R_0402
R6, R8: 200k; R_0402
U3: NVT2006BQ
U4: PCA9306
U5: ICM-20789
U6: MS5611-01BA

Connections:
1v8: R9.1, R10.1, U3.2 (VREFA), U4.2 (VREF1), U5.8 (VDDIO); also elsewhere on the board
3v3: C13.2, C15.2, R5.1, R6.1, R7.1, R8.1, U3.15 (VREFB), U4.7 (VREF2), U5.13 (VDD), U6.1 (VDD); also elsewhere on the board
/BARO_~CS: U6.4 (CSB), U6.5 (CSB); also elsewhere on the board
/IMU_INT: U3.10 (B5); also elsewhere on the board
/IMU_PR_CL: R5.2, U4.6 (SCL2); also elsewhere on the board
/IMU_PR_DA: R7.2, U4.5 (SDA2); also elsewhere on the board
/IMU_~CS: U3.11 (B4); also elsewhere on the board
/SPI3_MISO: U3.14 (B1), U6.6 (SDO); also elsewhere on the board
/SPI3_MOSI: U3.13 (B2), U6.7 (SDI/SDA); also elsewhere on the board
/SPI3_SCLK: U3.12 (B3), U6.8 (SCLK); also elsewhere on the board
GND: C13.1, C14.1, C15.1, C16.1, U3.1 (GND), U4.1 (GND), U5.10 (REGOUT), U5.11 (FSYNC), U5.18 (GND), U5.20 (NC), U6.2 (PS), U6.3 (GND); also elsewhere on the board
unnamed: C14.2, R6.2, U3.16 (EN)
unnamed: C16.2, R8.2, U4.8 (EN)
unnamed: R9.2, U4.3 (SCL1), U5.7 (PR_CL)
unnamed: R10.2, U4.4 (SDA1), U5.6 (PR_DA)
unnamed: U3.3 (A1), U5.23 (SCL/SCLK)
unnamed: U3.4 (A2), U5.9 (SDO/AD0)
unnamed: U3.5 (A3), U5.24 (SDA/SDI)
unnamed: U3.6 (A4), U5.22 (~CS)
unnamed: U3.7 (A5), U5.12 (INT)

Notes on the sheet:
SPI Level Shifter
Integrated IMU + Barometer
Redundant Barometer
I2C Level Shifter
7-DoF IMU

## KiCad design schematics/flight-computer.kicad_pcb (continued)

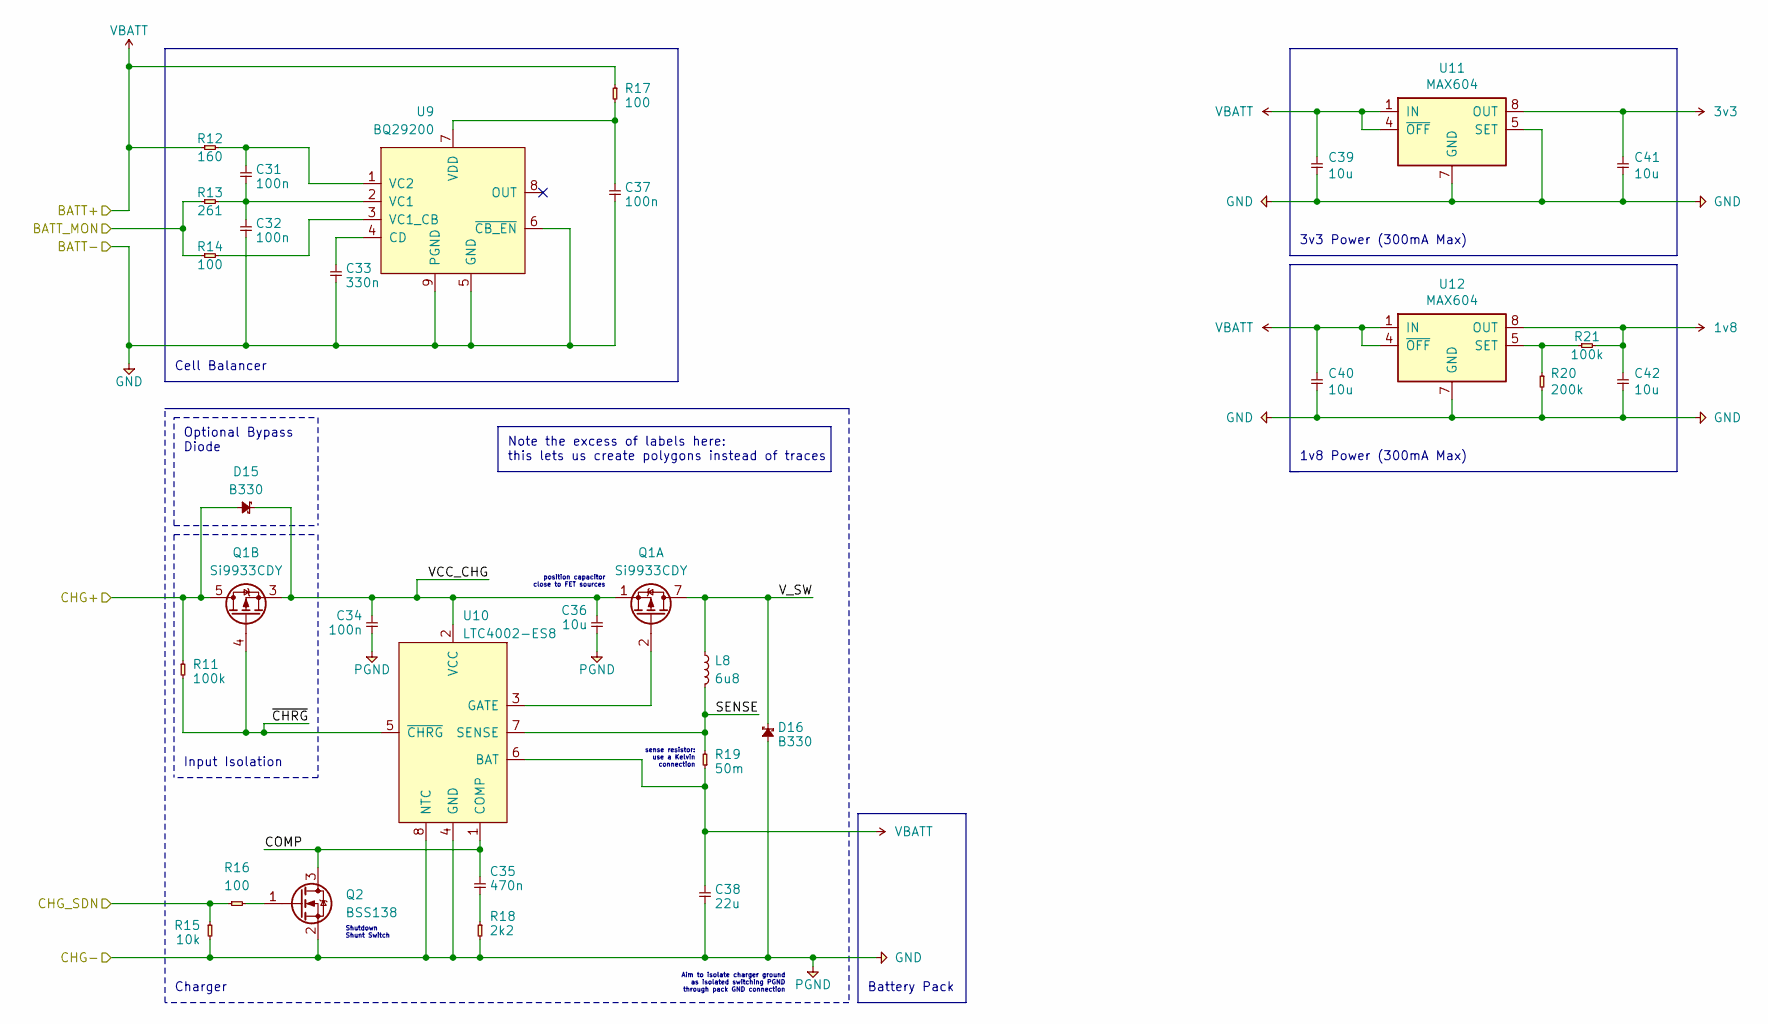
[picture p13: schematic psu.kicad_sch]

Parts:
C31, C32, C34, C37: 100n; C_0402; Farnell 1759166
C33: 330n; C_0402; Farnell 2346946
C35: 470n; C_0402; Farnell 2320847
C36: 10u; C_0402; Farnell 2611940
C38: 22u; C_0402; Farnell 2525135
C39, C40, C41, C42: 10u; C_0402
D15, D16: B330
L8: 6u8; L_Wuerth_HCI-7050
Q1: Si9933CDY; Farnell 1779275
Q2: BSS138
R11: 100k; R_0402; Farnell 2380290
R12: 160; R_0402; Farnell 2694996
R13: 261; R_0402; Farnell 2303485
R14, R17: 100; R_0402; Farnell 2447552
R15: 10k; R_0402; Farnell 1576464
R16: 100; R_0402; Farnell 2694996
R18: 2k2; R_0402; Farnell 1576464
R19: 50m; R_0402; Farnell 2008296
R20: 200k; R_0402
R21: 100k; R_0402
U9: BQ29200; Farnell 2383074
U10: LTC4002-ES8
U11, U12: MAX604

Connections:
1v8: C42.1, R21.2, U12.8 (OUT); also elsewhere on the board
3v3: C41.1, U11.8 (OUT); also elsewhere on the board
/CHG_SDN: R15.1, R16.1; also elsewhere on the board
/PSU/BATT_MON: R13.1, R14.1; also elsewhere on the board
/PSU/CHG+: D15.2, Q1.5 (D2), Q1.6 (D2), R11.1; also elsewhere on the board
/PSU/COMP: C35.1, Q2.3 (D), U10.1 (COMP)
/PSU/SENSE: L8.2, R19.2, U10.7 (SENSE)
/PSU/VCC_CHG: C34.1, C36.1, D15.1, Q1.1 (S1), Q1.3 (S2), U10.2 (VCC)
/PSU/V_SW: D16.1, L8.1, Q1.7 (D1), Q1.8 (D1)
/PSU/~CHRG: Q1.4 (G2), R11.2, U10.5 (~CHRG)
GND: C32.2, C33.2, C34.2, C36.2, C37.2, C38.2, C39.2, C40.2, C41.2, C42.2, D16.2, Q2.2 (S), R15.2, R18.2, R20.2, U9.5 (GND), U9.6 (~CB_EN), U9.9 (PGND), U10.4 (GND), U10.8 (NTC), U11.2 (GND), U11.3 (GND), U11.5 (SET), U11.6 (GND), U11.7 (GND), U12.2 (GND), U12.3 (GND), U12.6 (GND), U12.7 (GND); also elsewhere on the board
unnamed: C31.1, R12.2, U9.1 (VC2)
unnamed: C31.2, C32.1, R13.2, U9.2 (VC1)
unnamed: C33.1, U9.4 (CD)
unnamed: C35.2, R18.1
unnamed: C37.1, R17.2, U9.7 (VDD)
unnamed: Q1.2 (G1), U10.3 (GATE)
unnamed: Q2.1 (G), R16.2
unnamed: R14.2, U9.3 (VC1_CB)
unnamed: R20.1, R21.1, U12.5 (SET)
VBATT: C38.1, C39.1, C40.1, R12.1, R17.1, R19.1, U10.6 (BAT), U11.1 (IN), U11.4 (~OFF), U12.1 (IN), U12.4 (~OFF); also elsewhere on the board

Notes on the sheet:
Input Isolation
Battery Pack
Charger
sense resistor: use a Kelvin connection
Aim to isolate charger ground as isolated switching PGND through pack GND connection
Note the excess of labels here: this lets us create polygons instead of traces
Cell Balancer
Optional Bypass Diode
3v3 Power (300mA Max)
position capacitor close to FET sources
1v8 Power (300mA Max)
Shutdown Shunt Switch

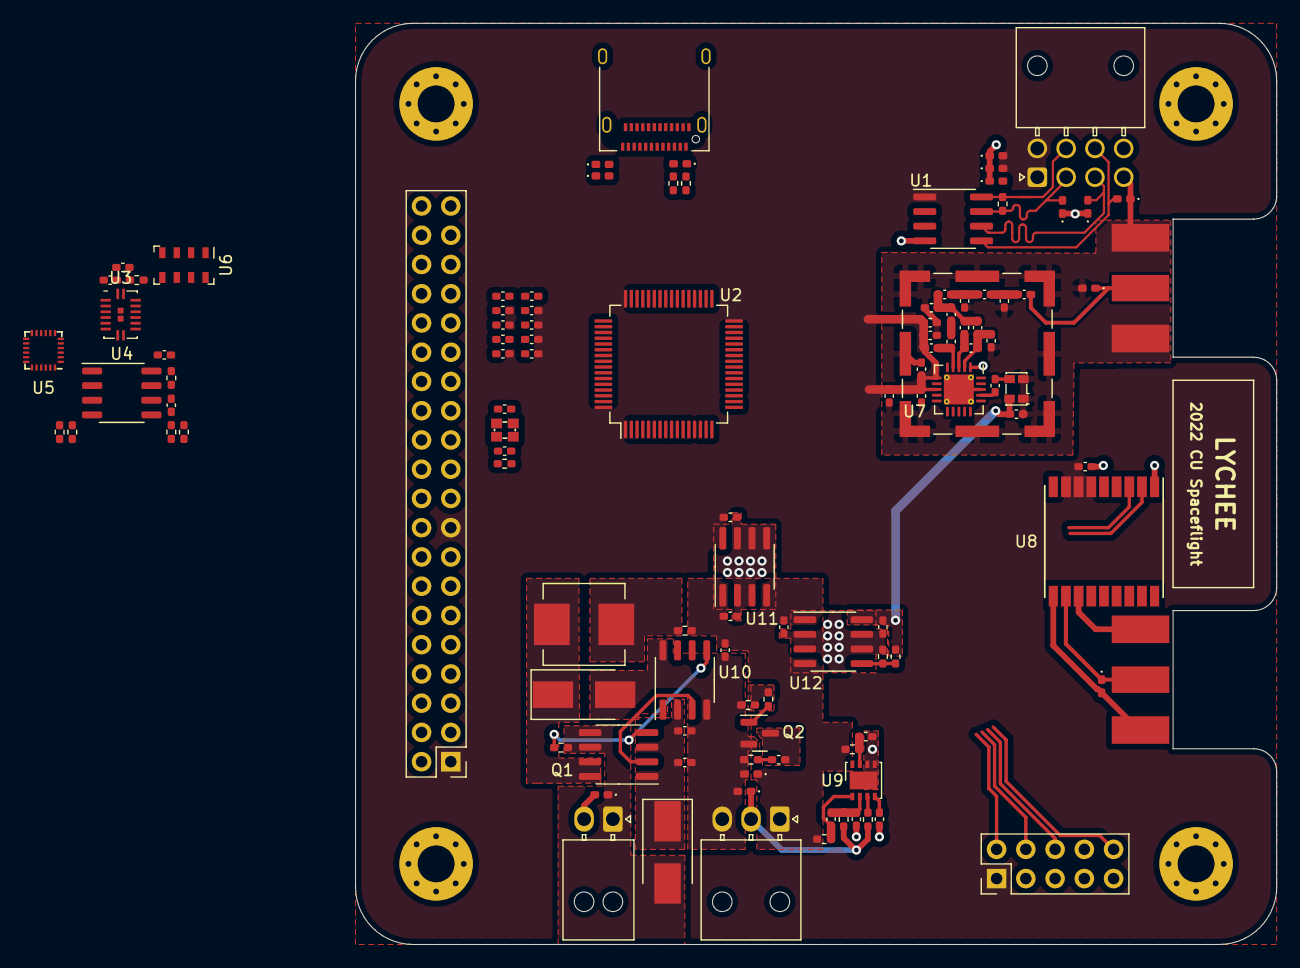
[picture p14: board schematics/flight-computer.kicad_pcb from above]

Board: 4 copper layers, 80.0 x 80.0 mm, 116 parts (0 on the bottom side), 75 nets.

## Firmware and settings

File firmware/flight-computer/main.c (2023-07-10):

/*
    ChibiOS - Copyright (C) 2006..2018 Giovanni Di Sirio

    Licensed under the Apache License, Version 2.0 (the "License");
    you may not use this file except in compliance with the License.
    You may obtain a copy of the License at

        http://www.apache.org/licenses/LICENSE-2.0

    Unless required by applicable law or agreed to in writing, software
    distributed under the License is distributed on an "AS IS" BASIS,
    WITHOUT WARRANTIES OR CONDITIONS OF ANY KIND, either express or implied.
    See the License for the specific language governing permissions and
    limitations under the License.
*/

#include "hal.h"
#include "ch.h"
#include "chprintf.h"

#include "mpu9250.h"
#include "ms5611.h"
#include "ublox.h"
#include "usbserial.h"

#if DEBUG
#include "debug.h"
#endif

/*
 * Application entry point.
 */
int main(void)
{

  /*
   * System initializations.
   * - HAL initialization, this also initializes the configured device drivers
   *   and performs the board-specific initializations.
   */
  halInit();
  chSysInit();

#if DEBUG
  DEBUG_INIT;

  /* Debug title block */
  /* This is designed to be a solid 40 char wide block */
  DEBUG_PRINTLN("                                        ");
  DEBUG_PRINTLN(" =======================================");
  DEBUG_PRINTLN(" == Lychee - High-Altitude Ballooning ==");
  DEBUG_PRINTLN(" =======================================");
  DEBUG_PRINTLN(" All work copyright 2022 CU Spaceflight ");
  DEBUG_PRINTLN("        Henry Franks & William Yu       ");
  DEBUG_PRINTLN(" =======================================");
  DEBUG_PRINTLN("                                        ");
#endif


  /* BEGIN INIT */
  //mpu9250_init();

#if ENABLE_BARO
  ms5611_init();
#endif

#if ENABLE_GPS
  ublox_init(&SD2);
#endif

#if ENABLE_USB
  usb_init();
#endif
  /*  END INIT  */

  /* START THREADS */
#if ENABLE_BARO
  ms5611_init_thd();
#endif

#if ENABLE_GPS
  ublox_thd_init();
#endif

#if ENABLE_USB
  usb_thd_init();
#endif

  while (true) {

    #if ENABLE_BARO
      ms5611_convert_d1(MS5611_OSR_4096);
      ms5611_adc_read();
    #endif

    //DEBUG_PRINT("0x%04x\r\n", mpu9250_fifo_count());

    chThdSleepMilliseconds(10);
  }
}

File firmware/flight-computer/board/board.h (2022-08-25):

/*
    ChibiOS - Copyright (C) 2006..2020 Giovanni Di Sirio

    Licensed under the Apache License, Version 2.0 (the "License");
    you may not use this file except in compliance with the License.
    You may obtain a copy of the License at

        http://www.apache.org/licenses/LICENSE-2.0

    Unless required by applicable law or agreed to in writing, software
    distributed under the License is distributed on an "AS IS" BASIS,
    WITHOUT WARRANTIES OR CONDITIONS OF ANY KIND, either express or implied.
    See the License for the specific language governing permissions and
    limitations under the License.
*/

/*
 * This file has been automatically generated using ChibiStudio board
 * generator plugin. Do not edit manually.
 */

#ifndef BOARD_H
#define BOARD_H

/*===========================================================================*/
/* Driver constants.                                                         */
/*===========================================================================*/

/*
 * Setup for Lychee board.
 */

/*
 * Board identifier.
 */
#define BOARD_Lychee
#define BOARD_NAME                  "Lychee"

/*
 * Board oscillators-related settings.
 * NOTE: LSE not fitted.
 */
#if !defined(STM32_LSECLK)
#define STM32_LSECLK                0U
#endif

#if !defined(STM32_HSECLK)
#define STM32_HSECLK                26000000U
#endif

/*
 * Board voltages.
 * Required for performance limits calculation.
 */
#define STM32_VDD                   330U

/*
 * MCU type as defined in the ST header.
 */
#define STM32F405xx

/*
 * IO pins assignments.
 */
#define GPIOA_UART4_TX              0U
#define GPIOA_UART4_RX              1U
#define GPIOA_USART2_TX             2U
#define GPIOA_USART2_RX             3U
#define GPIOA_BARO_CS               4U
#define GPIOA_SPI1_SCLK             5U
#define GPIOA_SPI1_MISO             6U
#define GPIOA_SPI1_MOSI             7U
#define GPIOA_I2C3_SCL              8U
#define GPIOA_OTG_FS_VBUS           9U
#define GPIOA_OTG_FS_ID             10U
#define GPIOA_OTG_FS_DP             11U
#define GPIOA_OTG_FS_DN             12U
#define GPIOA_SWDIO                 13U
#define GPIOA_SWCLK                 14U
#define GPIOA_PIN15                 15U

#define GPIOB_IMU_CS                0U
#define GPIOB_PIN1                  1U
#define GPIOB_PIN2                  2U
#define GPIOB_PIN3                  3U
#define GPIOB_PIN4                  4U
#define GPIOB_PIN5                  5U
#define GPIOB_I2C1_SCL              6U
#define GPIOB_I2C1_SDA              7U
#define GPIOB_PIN8                  8U
#define GPIOB_PIN9                  9U
#define GPIOB_USART3_TX             10U
#define GPIOB_USART3_RX             11U
#define GPIOB_RADIO_CS              12U
#define GPIOB_SPI2_SCLK             13U
#define GPIOB_SPI2_MISO             14U
#define GPIOB_SPI2_MOSI             15U

#define GPIOC_PIN0                  0U
#define GPIOC_PIN1                  1U
#define GPIOC_PIN2                  2U
#define GPIOC_CHG_SDN               3U
#define GPIOC_IMU_INT               4U
#define GPIOC_GPS_RESET             5U
#define GPIOC_RADIO_INT             6U
#define GPIOC_RADIO_SDN             7U
#define GPIOC_PIN8                  8U
#define GPIOC_I2C3_SDA              9U
#define GPIOC_SPI3_SCLK             10U
#define GPIOC_SPI3_MISO             11U
#define GPIOC_SPI3_MOSI             12U
#define GPIOC_PIN13                 13U
#define GPIOC_PIN14                 14U
#define GPIOC_PIN15                 15U

#define GPIOD_PIN0                  0U
#define GPIOD_PIN1                  1U
#define GPIOD_PIN2                  2U
#define GPIOD_PIN3                  3U
#define GPIOD_RESET                 4U
#define GPIOD_OVER_CURRENT          5U
#define GPIOD_PIN6                  6U
#define GPIOD_PIN7                  7U
#define GPIOD_PIN8                  8U
#define GPIOD_PIN9                  9U
#define GPIOD_PIN10                 10U
#define GPIOD_PIN11                 11U
#define GPIOD_LED4                  12U
#define GPIOD_LED3                  13U
#define GPIOD_LED5                  14U
#define GPIOD_LED6                  15U

#define GPIOE_INT1                  0U
#define GPIOE_INT2                  1U
#define GPIOE_PIN2                  2U
#define GPIOE_CS_SPI                3U
#define GPIOE_PIN4                  4U
#define GPIOE_PIN5                  5U
#define GPIOE_PIN6                  6U
#define GPIOE_PIN7                  7U
#define GPIOE_PIN8                  8U
#define GPIOE_PIN9                  9U
#define GPIOE_PIN10                 10U
#define GPIOE_PIN11                 11U
#define GPIOE_PIN12                 12U
#define GPIOE_PIN13                 13U
#define GPIOE_PIN14                 14U
#define GPIOE_PIN15                 15U
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

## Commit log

2021-11-07 Migrate remaining symbols to local library
    [altimeter.sch, flight-computer.kicad_pcb, flight-computer.sch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]
2021-12-14 Misc fixes
    [flight-computer.kicad_pcb, flight-computer.sch]
2021-12-14 Migrate to KiCad 6
    [altimeter.kicad_sch, altimeter.sch, flight-computer.kicad_pcb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]
2021-12-15 Complete revision 1 schematic
    [altimeter.kicad_sch, flight-computer.kicad_pcb, flight-computer.kicad_sch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]
2021-12-26 Add oscillators and clean up schematics
    [altimeter.kicad_sch, flight-computer.kicad_sch, psu.kicad_sch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]
2021-12-26 Fix broken symbol and footprint references
    [flight-computer.kicad_sch, psu.kicad_sch]
2021-12-26 Add missing IC footprints
    [altimeter.kicad_sch, flight-computer.kicad_pcb, flight-computer.kicad_sch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]
2021-12-26 Fix outdated footprint references in symbol lib
    [altimeter.kicad_sch, flight-computer.kicad_pcb, flight-computer.kicad_sch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]
2021-12-28 Preliminary board layout
    [altimeter.kicad_sch, flight-computer.kicad_pcb, flight-computer.kicad_sch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]
2021-12-28 Mark isolated PGND on schematic
    [flight-computer.kicad_sch, psu.kicad_sch]
2021-12-31 Rough power and RF layouts
    [flight-computer.kicad_pcb, flight-computer.kicad_sch, psu.kicad_sch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]
2021-12-31 Rename to Lychee
    [altimeter.kicad_sch, flight-computer.kicad_pcb, flight-computer.kicad_sch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]
2022-01-02 Fix broken model paths
    [flight-computer.kicad_pcb]
2022-01-06 Migrate to common Strix lib via submodule
    [altimeter.kicad_sch, flight-computer.kicad_pcb, flight-computer.kicad_sch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]
2022-01-07 Update layout and models
    [flight-computer.kicad_pcb, flight-computer.kicad_sch, psu.kicad_sch]
2022-01-11 Route oscillator
    [flight-computer.kicad_pcb, flight-computer.kicad_sch]
2022-01-12 Change peripheral interface assignments to match layout
    [flight-computer.kicad_pcb, flight-computer.kicad_sch]
2022-01-13 Route GPIO peripheral connections
    [flight-computer.kicad_pcb, flight-computer.kicad_sch]
2022-01-14 Fillet and stitch telemetry SMA feed
    [flight-computer.kicad_pcb]
2022-01-22 Change level shifter to open drain compliant chip
    [altimeter.kicad_sch, flight-computer.kicad_pcb, flight-computer.kicad_sch]
2022-01-23 Complete first draft
    [altimeter.kicad_sch, flight-computer.kicad_pcb, flight-computer.kicad_sch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]
2022-01-23 Add order codes for remaining components
    [altimeter.kicad_sch, flight-computer.kicad_sch, psu.kicad_sch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]
2022-01-24 Add test points
    [altimeter.kicad_sch, flight-computer.kicad_pcb, flight-computer.kicad_sch]
2022-01-24 Clean up silkscreen
    [flight-computer.kicad_pcb]
2022-01-26 Final changes for manufacture
    [flight-computer.kicad_pcb, flight-computer.kicad_sch]
2022-01-27 Add tildes into empty part no references
    [flight-computer.kicad_sch]
2022-01-30 Add blackbox board
    [blackbox.kicad_pcb, blackbox.kicad_sch]
2022-01-30 Clean up board
    [blackbox.kicad_pcb]
2022-01-30 Add power LED and test points
    [blackbox.kicad_pcb, blackbox.kicad_sch]
2022-01-30 Final changes for manufacture (and silkscreen meme)
    [blackbox.kicad_pcb, blackbox.kicad_sch]
2022-01-30 Fix library references
    [blackbox.kicad_pcb, blackbox.kicad_sch]
2022-03-07 Update passive order codes to 0402
    [blackbox.kicad_sch, flight-computer.kicad_sch, psu.kicad_sch]
2022-03-12 Minor changes to pass ERC
    [altimeter.kicad_sch, blackbox.kicad_sch, flight-computer.kicad_sch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]
2022-07-02 Fix driver import and remove old files
    [main.c]
2022-07-02 Configure debugger
    [board.cfg]
2022-08-01 Set up for GPS driver test
2022-08-17 Generate electrical docs
    [flight-computer.kicad_pcb]
2022-08-18 Update layout doc
    [flight-computer.kicad_pcb]
2022-08-18 Update PCB annotations and layout doc
    [flight-computer.kicad_pcb]
2022-08-19 Fix missing NC marker in PCB
    [flight-computer.kicad_pcb]
2022-08-20 Enable SPI subsystem
2022-08-21 Update drivers submodule and remove reference to old GPS debug flag
2022-08-22 Update config for new baro driver
2022-08-22 Update driver submodule reference for baro
2022-08-25 Add baro skeleton and test PROM read in main loop
    [board.cfg]
2022-09-03 Fix typo in schematic
    [flight-computer.kicad_sch]
